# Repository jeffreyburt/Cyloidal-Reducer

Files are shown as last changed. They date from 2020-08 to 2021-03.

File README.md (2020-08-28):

# Cyloidal-Reducer

CAD files for a 12:1 cycloidal reducer.           
BOM for CAD files:
Filament: I printed in PLA and had no major problems.
Stepper: I used a NEMA 17.
Bearings: Generic 0.625" OD 0.125" ID bearings.

Ok time for advice and know issues. First of all I'm don't fully recommend just using my designs, if possible design your own with some of my reccomendations.
All issues/tips starting from the bottom of the design:
The clearance between the bolt holes and the supports for the outer pin ring is not enough, the supports shoud be further from that hole to allow the bolt to fit properly. I was able to make it work, but it wasn't optimal.
Secondly, the outer ring and its supports are poorly designed for 3d printing, they required a huge ammount of support to print, you can probably design a more efficient way to support the pins. If you don't do that, it's slightly more efficient to print upside down (with the top of the pins on the print bed).
Next, the hole for the motor shaft on the primary input shaft was too small. I fixed this by scaling up the printing size in the slicer (worked out ok for me due to designing some wiggle room) but you may wan to change that.
Moving on the posts used to contain the bearings on the primary bearing assembly were a bit too small. I fixed this by just super gluing them into place. This wasn;t an issue on the uppermost bearing due to the input shaft being scaled up.
Second to last, the central cycloidal gear is too large when printed at 100% scale. I printed at 98.5% but you might be able to get away with less. Try to decrease it's size as little as possible as it leads to increased backlash.
Finally, the pins on the output shaft were slightly too large, leading to too much friction. I had to reprint with a smaller size (the change is in the CAD files so you should be fine, just be weary of this if you are designing from scratch).

Update 8/24/2020: I've done a bit more testing and I am less convinced that only the cyucloid size effects the backlash. I think the tolerance in the bearing block also has something to do with it. I will do some more testing and update further. 

Update 8/26/2020: After further testing I have concluded that printing the cycloid gear at 100% actually works and probably helps to reduce backlash though I still belive that the bearings contribute as well). A bit more testing is needed as the bearings don't totally work with the new cycloid. 

Update 8/27/2020: Yeah just print the main cycloid at 10% and make sure your bearing tolerance is correct. Once you have everything working, run the reducer for a while to break it in.

Here is the link to the feature script I used:https://forum.onshape.com/discussion/7567/cycloidal-gear-generator
Once everything is printed I recommend liberally greasing with vaseline/

Good luck! Please message me with any questions that you have.

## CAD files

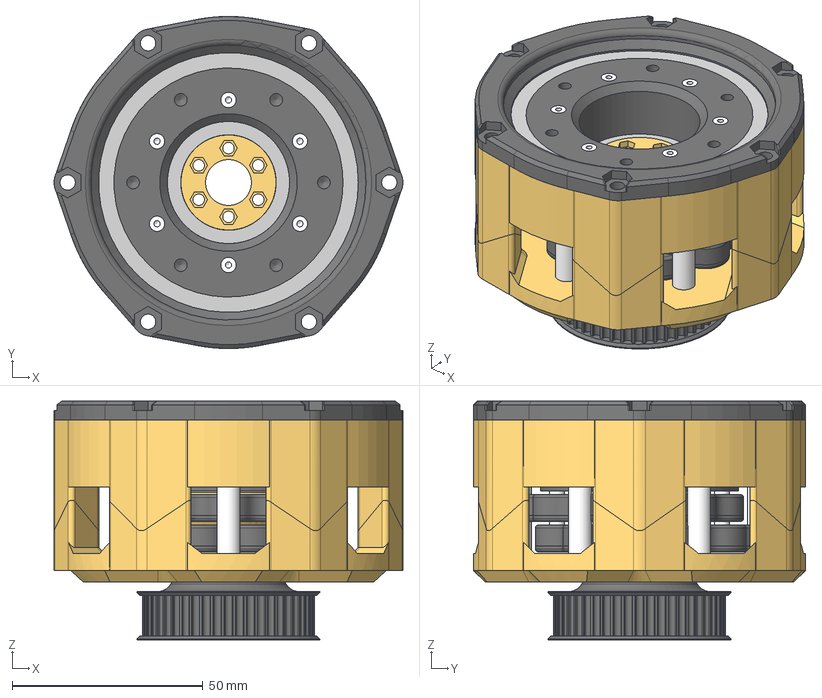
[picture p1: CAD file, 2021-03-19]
6th axis bare v8.step
91.4 x 87.0 x 62.6 mm
bearing
Inner pins
Disk body x 2
Cap x 2
snaller bearing x 4
pully
606 bearing
606 bearing v2
Bottom
Top
Outer pins 2
big bearing
cap_1
output

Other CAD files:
Final cycloidal .f3z
